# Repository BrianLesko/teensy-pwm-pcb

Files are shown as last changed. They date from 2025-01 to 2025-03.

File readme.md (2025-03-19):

# Teensy 4.0 PWM pcb

**My go-to board for servo motor and ESC control** 
This compact PCB design and 3dprinted mount brings power rails parallel to your teensy 4.0 microcontroller. Any 3-pin Futaba J connector can plug right into your teensy. Intended for use in robotics projects.

<div align="center">
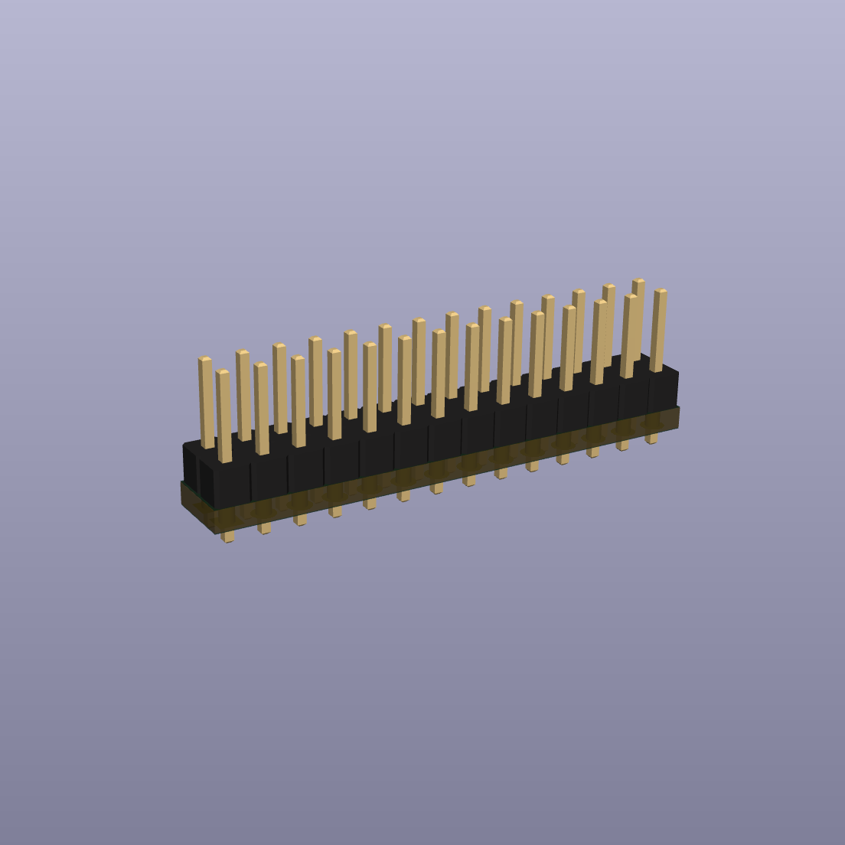
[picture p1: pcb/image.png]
PCB Image

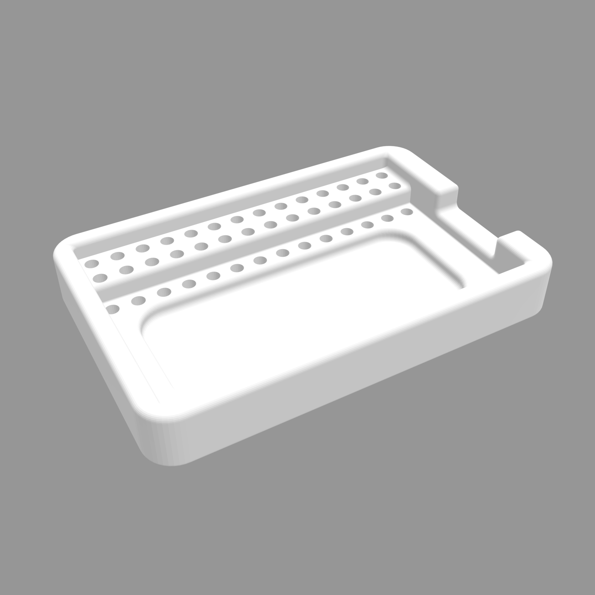
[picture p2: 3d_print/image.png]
3D Print Image

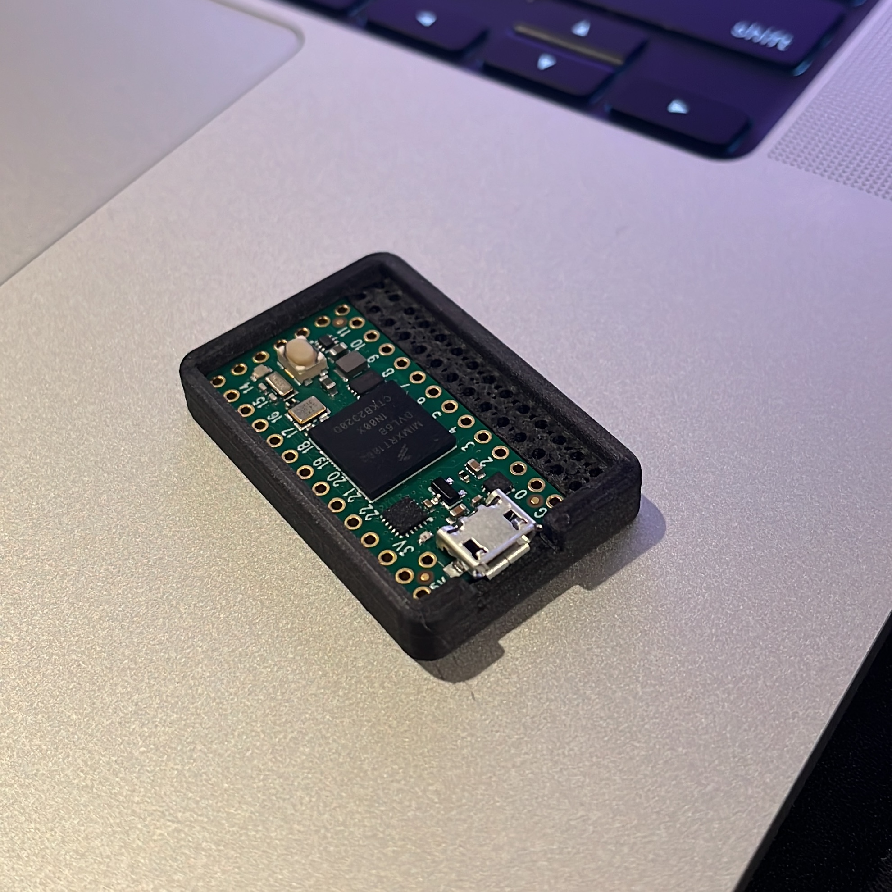
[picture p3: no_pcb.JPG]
photo of 3dprint and teensy

</div>

## Usage

materials:
- `The teensy 4.0`
- `3d printed mount`
- `pcb`
- `power source`
- `Futaba J connectors`

#### 1. Solder the pcb to two rows of headers.

#### 2. Print the mount.
- Because its small you might have to adjust the tolerances for your printer to fit the teensy.

#### 3. Solder one row of headers to the teensy. Make sure to do it on the right side of the teensy.

#### 4. Put the teensy and pcb in the mount.
- You might have to sand down the headers depending on the accuracy of your print.

#### 5. Connect ground on the pcb to the ground on the teensy.
<div align="center">
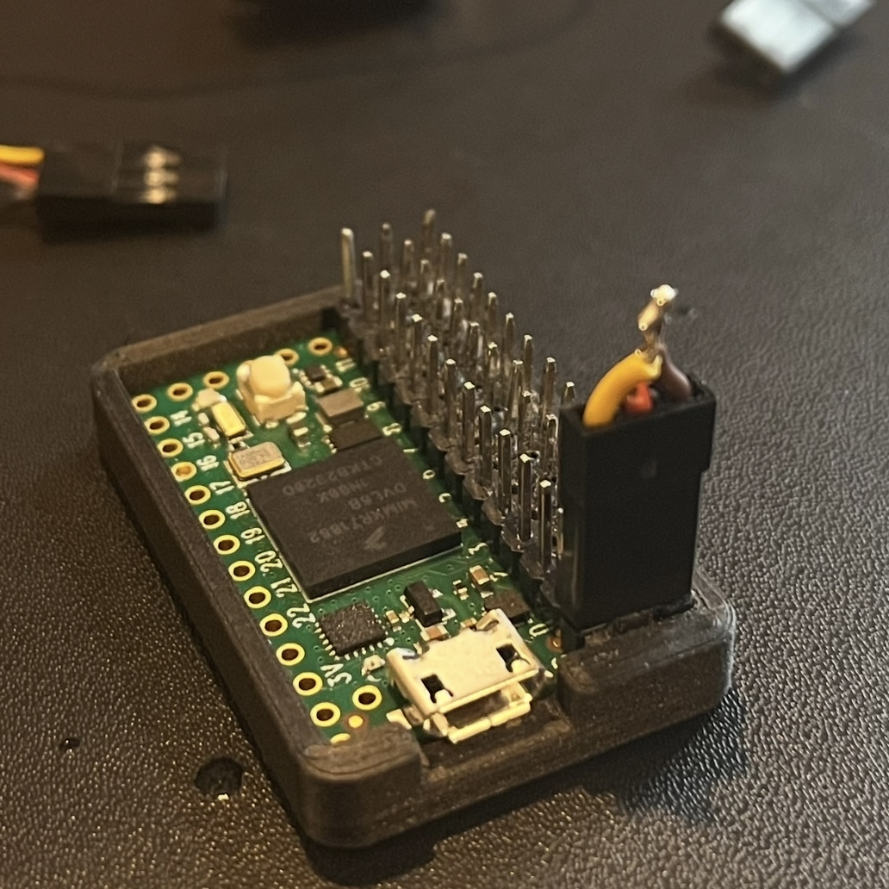
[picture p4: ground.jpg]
ground bus connected to teensy

</div>

#### 6. Add your power source to any set of pins on the teensy, connect your motors, and try out some pwm control.
- You can get started with the included `sketch.ino` file. 
- You'll need to [set up your teensy](https://www.pjrc.com/teensy/teensyduino.html) and install the [PWMservo](https://www.pjrc.com/teensy/td_libs_Servo.html) library. 
-Check out the result in test.mp4.

#### 7. Watch the demonstration video.
[Watch the demo on X](https://x.com/TheBrianLesko/status/1888679622583464144)

## Teensy 4.0

The [teensy 4.0](https://www.pjrc.com/store/teensy40.html) is a powerful microcontroller that can be used to control servos, ESCs, and other devices that require a pulse width modulated signal. 

## Why use a PCB

Sure, you ***could*** bend long headers and solder everything by hand, but that’s time-consuming and error-prone.

The pcb files were made with [KiCad](https://www.kicad.org) and exported to gerber files for [JLCPCB](https://jlcpcb.com).

## 3d Printed Mount 

The print needs high accuracy because this setup is so compact. Its smaller than most RC gyro units. 

## PWM 

pwm can be used to control servos, ESCs, and other devices that require a pulse width modulated signal.

[pwm](https://en.wikipedia.org/wiki/Pulse-width_modulation)

&nbsp;

<hr>

&nbsp;

<div align="center">

╭━━╮╭━━━┳━━┳━━━┳━╮╱╭╮        ╭╮╱╱╭━━━┳━━━┳╮╭━┳━━━╮
┃╭╮┃┃╭━╮┣┫┣┫╭━╮┃┃╰╮┃┃        ┃┃╱╱┃╭━━┫╭━╮┃┃┃╭┫╭━╮┃
┃╰╯╰┫╰━╯┃┃┃┃┃╱┃┃╭╮╰╯┃        ┃┃╱╱┃╰━━┫╰━━┫╰╯╯┃┃╱┃┃
┃╭━╮┃╭╮╭╯┃┃┃╰━╯┃┃╰╮┃┃        ┃┃╱╭┫╭━━┻━━╮┃╭╮┃┃┃╱┃┃
┃╰━╯┃┃┃╰┳┫┣┫╭━╮┃┃╱┃┃┃        ┃╰━╯┃╰━━┫╰━╯┃┃┃╰┫╰━╯┃
╰━━━┻╯╰━┻━━┻╯╱╰┻╯╱╰━╯        ╰━━━┻━━━┻━━━┻╯╰━┻━━━╯

&nbsp;

<a href="https://x.com/TheBrianLesko/">X Logo</a> &nbsp; &nbsp; &nbsp; &nbsp; &nbsp; &nbsp; <a href="https://github.com/BrianLesko">GitHub</a> &nbsp; &nbsp; &nbsp; &nbsp; &nbsp; &nbsp; <a href="https://www.linkedin.com/in/brianlesko/">LinkedIn</a>

follow all of these for pizza :)

</div>

&nbsp;

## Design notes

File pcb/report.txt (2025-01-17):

Warning: Width correction constrained.  The width correction value must be in the range of [0.000001 mm; 0.199999 mm] for the current design rules.
Plotted to '/Users/brianlesko/Documents/test/pwm_power/pwm_power-F_Cu.gbr'.
Plotted to '/Users/brianlesko/Documents/test/pwm_power/pwm_power-B_Cu.gbr'.
Plotted to '/Users/brianlesko/Documents/test/pwm_power/pwm_power-F_Paste.gbr'.
Plotted to '/Users/brianlesko/Documents/test/pwm_power/pwm_power-B_Paste.gbr'.
Plotted to '/Users/brianlesko/Documents/test/pwm_power/pwm_power-F_Mask.gbr'.
Plotted to '/Users/brianlesko/Documents/test/pwm_power/pwm_power-B_Mask.gbr'.
Plotted to '/Users/brianlesko/Documents/test/pwm_power/pwm_power-Edge_Cuts.gbr'.
Created Gerber job file '/Users/brianlesko/Documents/test/pwm_power/pwm_power-job.gbrjob'.
Plotted to '/Users/brianlesko/Documents/test/pwm_power/pwm_power-F_Cu.gbr'.
Plotted to '/Users/brianlesko/Documents/test/pwm_power/pwm_power-B_Cu.gbr'.
Plotted to '/Users/brianlesko/Documents/test/pwm_power/pwm_power-F_Paste.gbr'.
Plotted to '/Users/brianlesko/Documents/test/pwm_power/pwm_power-B_Paste.gbr'.
Plotted to '/Users/brianlesko/Documents/test/pwm_power/pwm_power-F_Mask.gbr'.
Plotted to '/Users/brianlesko/Documents/test/pwm_power/pwm_power-B_Mask.gbr'.
Plotted to '/Users/brianlesko/Documents/test/pwm_power/pwm_power-Edge_Cuts.gbr'.
Created Gerber job file '/Users/brianlesko/Documents/test/pwm_power/pwm_power-job.gbrjob'.
Info: Done.
Info: Done.

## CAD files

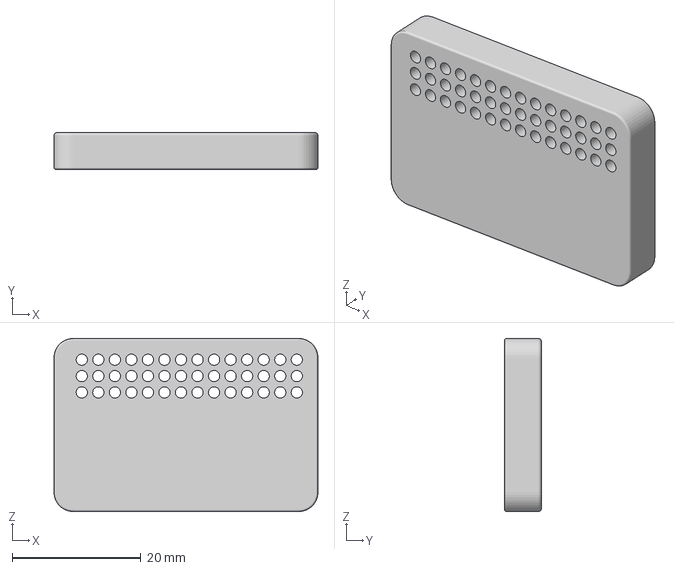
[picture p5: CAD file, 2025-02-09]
3d_print/teensy 4 holder v6.3mf
41.0 x 5.75 x 26.9 mm

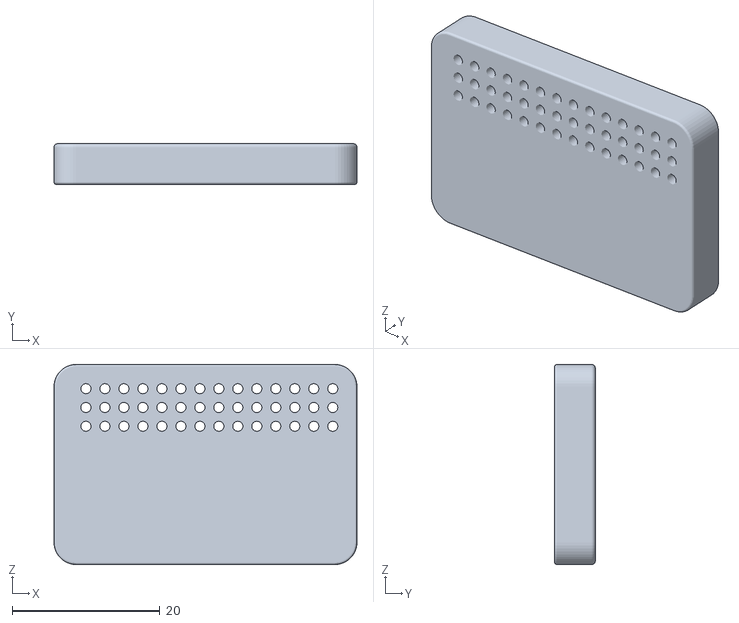
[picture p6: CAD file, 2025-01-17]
3d_print/v3 (no pcb)/teensy_holder.stl
41.0 x 5.50 x 27.1

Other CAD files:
3d_print/teensy 4 holder v6.dwg
3d_print/teensy 4 holder v6.f3d
3d_print/teensy 4 holder v6.stl
3d_print/v3 (no pcb)/teensy_holder v3.f3d

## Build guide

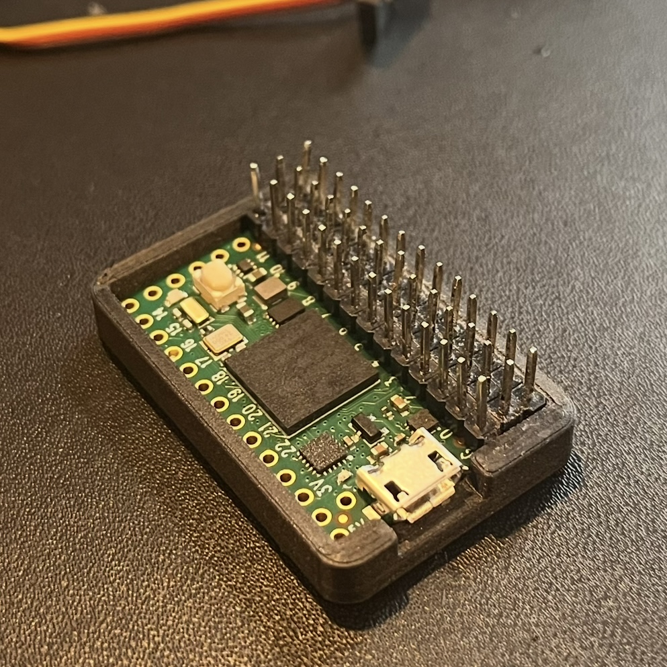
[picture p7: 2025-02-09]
assembled.jpg

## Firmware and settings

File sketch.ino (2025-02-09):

#include <PWMServo.h>

//create servo objects
PWMServo servo1;
PWMServo servo2;
PWMServo servo3;
PWMServo servo4;
PWMServo servo5;
PWMServo servo6;
PWMServo servo7;
PWMServo servo8;
PWMServo servo9;
PWMServo servo10;

// the setup function runs once when you press reset or power the board
void setup() {

  pinMode(LED_BUILTIN, OUTPUT);
  Serial.begin(38400);

  pinMode(5, OUTPUT);
  servo1.attach(5);
  servo1.write(150);

  pinMode(6, OUTPUT);
  servo2.attach(6);
  servo2.write(95);

  pinMode(7, OUTPUT);
  servo3.attach(7);
  servo3.write(95);

  pinMode(8, OUTPUT);
  servo4.attach(8);
  servo4.write(95);

  pinMode(9, OUTPUT);
  servo5.attach(9);
  servo5.write(95);

  pinMode(10, OUTPUT);
  servo6.attach(10);
  servo6.write(95);

  pinMode(11, OUTPUT);
  servo7.attach(11);
  servo7.write(95);

  pinMode(12, OUTPUT);
  servo8.attach(12);
  servo8.write(95);
  
}

// the loop function runs over and over again forever
void loop() {

  Serial.println("Hello World");

  servo1.write(30);
  servo2.write(30);
  servo3.write(30);
  servo4.write(30);
  servo5.write(30);
  servo6.write(30);
  servo7.write(30);
  servo8.write(30);
  digitalWrite(LED_BUILTIN, HIGH);  // turn the LED on (HIGH is the voltage level)
  delay(1000);

  servo1.write(125);                  // wait for a second
  servo2.write(125);  
  servo3.write(125);  
  servo4.write(125); 
  servo5.write(125);
  servo6.write(125);
  servo7.write(125);
  servo8.write(125);

  digitalWrite(LED_BUILTIN, LOW);   // turn the LED off by making the voltage LOW
  delay(1000);                      // wait for a second
}

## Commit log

2025-01-24 added drill holes
    [pwm_power-B_Mask.gbr, pwm_power-B_Paste.gbr, pwm_power-Edge_Cuts.gbr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]
2025-02-09 working test with servo motors
    [teensy 4 holder v6.3mf, teensy 4 holder v6.dwg, teensy 4 holder v6.f3d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]
